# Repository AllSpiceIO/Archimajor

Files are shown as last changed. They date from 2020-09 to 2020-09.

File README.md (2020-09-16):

**Note**: The information contained below does not necessarily reflect the design intent for this board, nor the true characteristics of the design. Rather, this is intended to be a proof of concept for electrical project architecture.




[*](./README.md#Disclaimer)

# Archimajor

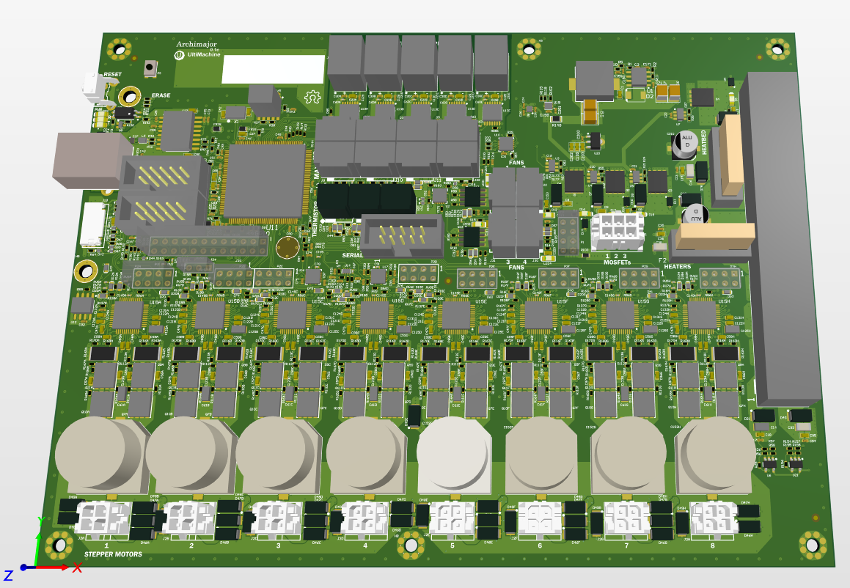
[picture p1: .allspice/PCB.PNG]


## Summary

3D printer motherboard, designed by [Ultimachine](https://ultimachine.com/). Features include:

- **5x integrated 256 microstep motor drivers**
- **6x PWM Mosfet outputs**
- **4x thermistor inputs**
- **SPI (Serial Peripheral Interface)**

---

## Specifications

### General Specifications

**Input Power Supply**: 12V - 24V DC, 16A+

**Operating Temperature Range (est.)**: 0dC ~ 70dC

## Firmware

[Source](https://github.com/ultimachine/Marlin4due/tree/Archim2)

[Binary](https://github.com/MarlinFirmware/Marlin/archive/bugfix-2.0.x.zip)

## Bill of Materials

<details>
    <summary><b>[Click to show Bill of Materials]</b></summary>

| Description | Designator | Footprint | Quantity | MANUFACTURER # |
|---|---|---|---|---|
| CAP CER 0603 100nF 50V 10% X7R | C1, C15, C18, C23A, C23B, C23C, C23D, C23E, C36, C47A, C47B, C47C, C47D, C47E, C47F, C47G, C47H, C95, C121A, C121B, C121C, C121D, C121E, C121F, C121G, C121H, C122A, C122B, C122C, C122D, C122E, C122F, C122G, C122H, C199, C202, C203 | C0603 | 37 | C0603C104K5RACTU |
| CAP CER 0.1UF 6.3V 10% X5R 0201 | C2, C60A, C60B, C60C, C60D, C60E, C62A, C62B, C62C, C62D, C62E, C67, C78, C91, C100, C105, C106, C149A, C149B, C149C, C149D, C149E, C149F, C149G, C149H, C204, C205, C206, C207, C208, C215, C217 | C0201 Large Pads | 32 | CL03A104KQ3NNNC |
| CAP CER 0402 TBD | C3 | C0402 | 1 | TBD |
| CAP CER 47UF 10V X5R 1210 | C4, C5 | C1210 | 2 | GRM32ER61A476KE20L |
| CAP CER 4.7UF 50V X7R 1210 | C6, C7 | C1210 | 2 | GRM32ER71H475KA88L |
| Capacitor Non Polarized | C8, C9, C10, C11, C27, C50, C153, C154, C209, C211 | C0603 | 10 | DNI-C0603TBD |
| CAP CER 10nF 50V X7R 0402 | C12A, C12B, C12C, C12D, C12E, C30A, C30B, C30C, C30D, C30E, C40, C43, C71, C77, C84, C86, C157, C158, C159, C160, C171, C214, C216 | C0402 | 23 | GRM155R71H103JA88D |
| 1000pF 50V Ceramic Capacitor X7R 0402 (1005 Metric) 0.039 L x 0.020 W (1.00mm x 0.50mm) | C13, C17, C35, C94 | C0402 | 4 | GRM155R71H102KA01D |
| CAP CER 10UF 50V 10% X5R 1206 | C14, C16, C38, C93 | C1206 | 4 | 490-10756-2-ND |
| CAP CER 0402 100nF 16V 10% X7R | C19, C20, C21, C22, C26, C28, C29, C31, C33, C39, C44, C45, C46, C51, C52, C54, C56, C63, C65, C66, C68, C69, C73, C76, C80, C81, C82, C92, C103, C155, C156, C161, C162, C164, C165, C166, C167, C169, C200, C201, C212, C213 | C0402 | 42 | GRM155R71C104KA88D |
| CAP CER 0402 1uF 6.3V 10% X5R | C24, C32, C34 | C0402 | 3 | GRM155R60J105KE19D |
| CAP ALUM 100UF 35V 20% SMD | C25, C210 | CAP-ELEC-063063077 | 2 | UWT1V101MCL1GS |
| CAP CER 10UF 6.3V 10% JB 0603 | C37, C53, C55, C57, C70, C72 | C0603 | 6 | C1608JB0J106K080AB |
| CAP CER 3PF 50V NP0 0603 | C41, C42 | C0603 | 2 | CL10C030BB8NNNC |
| CAP CER 0.22UF 50V X7R 0603 | C48A, C48B, C48C, C48D, C48E, C48F, C48G, C48H, C59A, C59B, C59C, C59D, C59E, C59F, C59G, C59H, C98A, C98B, C98C, C98D, C98E, C98F, C98G, C98H, C99A, C99B, C99C, C99D, C99E, C99F, C99G, C99H | C0603 | 32 | CGA3E3X7R1H224K080AB |
| CAP CER 10PF 50V 5% NP0 0402, 470nF 6.3v C0402 - GRM155R60J474KE19D | C49, C132A, C132B, C132C, C132D, C132E, C132F, C132G, C132H | C0402 | 9 | CL05C100JB5NNNC, GRM155R60J474KE19D |
| CAP CER 0603  1nF 50v 10% X7R | C58A, C58B, C58C, C58D, C58E, C58F, C58G, C58H, C96A, C96B, C96C, C96D, C96E, C96F, C96G, C96H, C97A, C97B, C97C, C97D, C97E, C97F, C97G, C97H, C123A, C123B, C123C, C123D, C123E, C123F, C123G, C123H | C0603 | 32 | C0603C102K5RACTU |
| CAP CER 1206 4.7uF 50V 10% X5R | C61A, C61B, C61C, C61D, C61E, C61F, C61G, C61H, C125A, C125B, C125C, C125D, C125E, C125F, C125G, C125H | C1206 | 16 | C1206C475K5PACTU |
| CAP CER 0402 TBD | C64, C74, C75, C79, C83, C85, C87, C88, C89, C90, C101, C102, C104 | C0402 | 13 | TBD |
| CAP CER 0.022UF 100V X7R 0603 | C124A, C124B, C124C, C124D, C124E, C124F, C124G, C124H | C0603 | 8 | C0603C223K1RACTU |
| CAP CER 4.7UF 6.3V X7R 0603 | C131A, C131B, C131C, C131D, C131E, C131F, C131G, C131H | C0603 | 8 | CL10B475KQ8NQNC |
| CAP CER 0402 2.2nF 25V C0G | C150 | C0402 | 1 | C0402C222J3GACTU |
| CAP CER 0402 22pF 50V 5% C0G | C151 | C0402 | 1 | 04025A220JAT2A |
| CAP ALUM 470UF 20% 50V SMD | C152A, C152B, C152C, C152D, C152E, C152F, C152G, C152H | CAP16x17 | 8 | UCZ1H471MNQ1MS |
| Capacitor Non Polarized | C198 | C0402 | 1 | DNI-C0402TBD |
| TVS DIODE 3.3VWM 10.4VC SOD923 | D1, D3, D13, D32, D33, D34, D35, D42, D58, D59, D64, D65, D66, D67, D68, D69, D71, D72, D73 | SOD923-100X40-2N | 19 | ESD9X3.3ST5G |
| DIODE SCHOTTKY 40V 5A SMB_DO214AA | D2 | SMB_DO-214AA_LRG | 1 | SK54B-LTP |
| DIODE TVS | D4, D10, D11, D14, D26 | SOD323-R | 5 | RSB39VTE-17 |
| DIODE SCHOTTKY 30V 200MA SOD523 | D5, D12A, D12B, D12C, D12D, D12E, D12F, D12G, D12H, D19A, D19B, D19C, D19D, D19E, D19F, D19G, D19H, D20A, D20B, D20C, D20D, D20E, D20F, D20G, D20H, D28, D29, D30, D31, D36, D37, D38, D39, D40, D41, D50, D51, D52, D53, D54, D55, D56, D57, D60, D61, D62, D63, D70, D74, D75, D76, D77 | SOD523_IPC | 52 | BAT54WX-TP |
| DIODE Schottky 3A SMA | D6, D7, D8, D15 | SMA-SM | 4 | SK310A |
| LED 0805 Red | D9, D16, D17, D18, D24, LED1, LED2, LED3, LED4 | LED2012120 | 9 | 5988110107F |
| TVS DIODE 24V 38.9V SMA | D21, D22, D43, D46A, D46B, D46C, D46D, D46E, D46F, D46G, D46H, D47A, D47B, D47C, D47D, D47E, D47F, D47G, D47H, D48A, D48B, D48C, D48D, D48E, D48F, D48G, D48H, D49A, D49B, D49C, D49D, D49E, D49F, D49G, D49H, D78 | SMA-SM | 36 | SMAJ24A |
| LED 0805 Green | D23 | LED2012120 | 1 | 5988170107F |
| LED 0805 Yellow | D25 | LED2012120 | 1 | 5988140107F |
| Rail-to-rail ESD protection devices | D27 | SOT886 | 1 | PRTR5V0U2F,115 |
| TVS DIODE 3.3VWM 10.4VC SOD923 | D44 | SOD923-D | 1 | ESD9X3.3ST5G |
| TVS DIODE 5V 9V SOD923 | D45 | SOD923-D | 1 | DF2S6.8FS,L3M |
| FUSE PTH ATO | F1, F2 | 3557 | 2 | 3557-2 |
| FERRITE BEAD 120 OHM 0603 1LN | FB26, FB27, FB28, FB29, FB30 | FB0603 | 5 | CIS10P121AC |
 | | FD1, FD2, FD3, FD4, FD5, FD6, FD7 | FIDUCIAL-1X2 | 7 | NOTAPART-Fiducial |
| Conn - 3mm Pitch Fixed | J1 | 43045-0612 | 1 | 0430450612 |
| Conn - 3mm Pitch Fixed | J2A, J2B, J2C, J2D, J2E, J2F, J2G, J2H | 43045-0412 | 8 | 43045-0412 |
| CONN BARRIER STRIP 10CIRC 0.325 | J3 | CON-Barrier-10-8.26mm | 1 | 4DB-P108-10 |
| 20021121-00010C4LF | J4 | FTSH-105-XX-X-DV | 1 | 20021121-00010C4LF |
| 3 Positions Header, Shrouded Connector 0.100 (2.54mm) Through Hole Gold - Pin in Paste | J5, J6, J7, J9, J10, J11, J22, J29, J30, J31, J32, J33 | 70543-02 PIN-IN-PASTE | 12 | 0705430002 |
 | | J8 | PN61729 | 1 | 61729-0010BLF |
| CONN HEADER VERT 10POS GOLD | J12, J13, J28 | HDR2X5 IDC | 3 | 302-S101 |
| Connector 2pos - Pin in Paste | J14, J15, J16 | 70543-01 PIN-IN-PASTE | 3 | 0705430001 |
| microSD 0475710001Molex Part | J18 | SD_MICRO 475710001 | 1 | 0475710001 |
| Header, 12-Pin, Dual row | J20 | HDR2X12 | 1 | 2213S-24G |
| TERM BLOCK 2POS 45DEG 3.5MM PCB | J21A, J21B, J21C, J21D, J21E | 1864286 | 5 | 1864286 |
| Header 3Pin 1Row T-Hole | J24 | HDR3X1 | 1 | 2211S-03G |
| FIXED IND 4.7UH 10A 15.5 MOHM | L1 | IND_10X10 | 1 | SRP1038A-4R7M |
| Common Mode Chokes Dual 90Ohm 100MHz 330mA 350mOhm DCR SMD | L5 | DLW21HN900SQ2L | 1 | DLW21HN900SQ2L |
| Header, 4-Pin, Dual row | P1, P2A, P2B, P2C, P2D, P2E, P2F, P2G, P2H | HDR2X4 | 9 | 2213S-08G, [NoParam] |
| MOSFET N-CH 40V 100A 8VSON | Q1, Q2, Q3, Q4 | SOT669_Universal | 4 | CSD18503Q5A |
| 40V 17 MOHM T6 S08FL DUAL | Q7A, Q7B, Q7C, Q7D, Q7E, Q7F, Q7G, Q7H, Q9A, Q9B, Q9C, Q9D, Q9E, Q9F, Q9G, Q9H, Q10A, Q10B, Q10C, Q10D, Q10E, Q10F, Q10G, Q10H, Q11A, Q11B, Q11C, Q11D, Q11E, Q11F, Q11G, Q11H | SO8FL-Dual | 32 | NVMFD5C478NT1G |
| TRANS NPN 60V 0.2A SOT523 | Q8 | SOT523 SMALL | 1 | MMBT3904T-7-F |
 | | Q12, Q13 | NCV8402AD-SOIC8 | 2 | NCV8402ADDR2G |
| RES SMD 10.2K OHM 1% 1/16W 0402 | R1 | R0402 | 1 | RC0402FR-0710K2L |
| RES SMD 1.4K OHM 1% 1/16W 0402 | R2 | R0402 | 1 | RMCF0402FT1K40 |
| RES 47 OHM 1% 1/16W 0402 | R3, R4, R13, R32, R59, R84, R86A, R86B, R86C, R86D, R86E, R86F, R86G, R86H, R88A, R88B, R88C, R88D, R88E, R89, R93, R94, R116A, R116B, R116C, R116D, R116E, R116F, R116G, R116H, R163A, R163B, R163C, R163D, R163E, R163F, R163G, R163H, R168A, R168B, R168C, R168D, R168E, R168F, R168G, R168H, R170A, R170B, R170C, R170D, R170E, R170F, R170G, R170H | R0402 | 54 | CRCW040247R0FKEDC |
| RES SMD 1.96K OHM 1% 1/16W 0402 | R5 | R0402 | 1 | RC0402FR-071K96L |
| RES SMD 10K OHM 1% 1/16W 0402 | R6, R7, R8, R9, R11, R12, R14, R15, R29, R30, R39, R54, R56, R64, R65, R66, R67, R68, R69, R70, R85, R95, R96, R97, R100, R101, R119, R150, R151, R155, R171, R182, R183 | R0402 | 33 | RC0402FR-0710KP |
| RES SMD 37.4K OHM 1% 1/16W 0402 | R10 | R0402 | 1 | RC0402FR-0737K4L |
| RES SMD 4.7K OHM 1% 1/16W 0402 | R16A, R16B, R16C, R16D, R16E, R16F, R16G, R16H, R18A, R18B, R18C, R18D, R18E, R18F, R18G, R18H, R62, R80, R90 | R0402 | 19 | RC0402FR-074K7L |
| Resistor | R17A, R17B, R17C, R17D, R17E, R17F, R17G, R17H, R60 | R0402 | 9 | DNI-R0402TBD |
| RES 0402 1k 63mW 1%, RES SMD 1K OHM 1% 1/16W 0402 | R19, R23, R33, R34, R36, R40, R41, R71, R72, R74, R76, R79, R102, R108A, R108B, R108C, R108D, R108E, R108F, R108G, R108H, R152, R174, R175, R176, R177, R186, R187, R188, R189, R191, R193, R197, R198 | R0402 | 34 | RC0402FR-071KL |
| RES SMD 100 OHM 1% 1/16W 0402 | R20, R21, R25, R53, R98, R99, R109, R114, R120, R133, R134, R135, R136, R137, R138, R139, R140, R141, R142, R143, R144, R145, R149, R153, R159, R160, R161, R180, R181 | R0402 | 29 | RC0402FR-07100RL |
| RES SMD 100K OHM 1% 1/16W 0402 | R22, R31, R35, R37, R38, R51, R58, R63, R73, R75, R78, R158, R190, R192 | R0402 | 14 | RC1005F104CS |
| RES SMD 10 OHM 1% 1/16W 0402 | R24, R27, R52, R55, R110A, R110B, R110C, R110D, R110E, R110F, R110G, R110H, R111A, R111B, R111C, R111D, R111E, R111F, R111G, R111H, R112A, R112B, R112C, R112D, R112E, R112F, R112G, R112H, R113A, R113B, R113C, R113D, R113E, R113F, R113G, R113H, R164A, R164B, R164C, R164D, R164E, R164F, R164G, R164H, R165A, R165B, R165C, R165D, R165E, R165F, R165G, R165H, R166A, R166B, R166C, R166D, R166E, R166F, R166G, R166H, R167A, R167B, R167C, R167D, R167E, R167F, R167G, R167H | R0402 | 68 | RC0402FR-0710RL |
| RES SMD 24K OHM 1% 1/16W 0402 | R26, R154 | R0402 | 2 | CRCW040224K0FKEDC |
| RES 0402 1M 100mW 5% | R28, R156 | R0402 | 2 | ERJ2GEJ105X |
| Res Thick Film 0402 24 Ohm 1% 0.063W | R42, R43, R45, R46, R47, R48, R77, R82, R83 | R0402 | 9 | RC0402FR-0724RL |
| RES SMD 2.37K OHM 1% 1/16W 0402 | R44, R50, R81, R87, R91, R92 | R0402 | 6 | RC0402FR-072K37L |
| RES SMD 6.8K OHM 1% 1/16W 0402 | R49 | R0402 | 1 | CRCW04026K80FKED |
| RES SMD 130K OHM 5% 1/16W 0402 | R57, R157 | R0402 | 2 | RC0402JR-07130KL |
| RES 0402 1M 100mW 5% | R61 | R0402TBD | 1 | ERJ2GEJ105X |
| RES SMD 0.0OHM JUMPER 1/10W 0603 | R103 | R0603 | 1 | CR0603-J/-000ELF |
| RES SMD 2.2 OHM 5% 1/16W 0402 | R107A, R107B, R107C, R107D, R107E, R107F, R107G, R107H | R0402 | 8 | RC0402JR-072R2L |
| RES SMD 15K 1% 1/16W 0402 | R115 | R0402 | 1 | RC1005F153CS |
| RES 0.01 OHM 1% 1/2W 0805 | R148 | R0805 | 1 | KRL1220E-M-R010-F-T5 |
| RES 0.05 OHM 1% 2W 2512 | R162A, R162B, R162C, R162D, R162E, R162F, R162G, R162H, R169A, R169B, R169C, R169D, R169E, R169F, R169G, R169H | R2512 | 16 | CSRN2512FK50L0 |
| RES SMD 1.8K OHM 1% 1/16W 0402 | R172, R173, R184, R185 | R0402 | 4 | RC0402FR-071K8L |
| VARISTOR 6.8V 10A 0201 | RV1, RV2, RV3, RV4, RV5A, RV5B, RV5C, RV5D, RV5E, RV5F, RV5G, RV5H, RV6A, RV6B, RV6C, RV6D, RV6E, RV6F, RV6G, RV6H, RV7A, RV7B, RV7C, RV7D, RV7E, RV7F, RV7G, RV7H | C0201 Large Pads | 28 | AVRM0603C6R8NT101N |
| SWTCH Momentary Washable | S1 | B3F-31XX | 1 | 1571610-2 |
| SWITCH TACTILE SPST-NO 0.05A 12V | S2 | KMR 6 Series | 1 | KMR741NG ULC LFS |
| IC REG BUCK ADJ 5A 8SOPWRPAD | U1 | SOIC127P600X170_HS | 1 | TPS54531DDAR |
| Quadruple Bus Buffer Gates With 3-State Outputs 14-VQFN -40 to 125 | U2, U10 | QFN50P350X350X100 | 2 | SN74AHCT125RGYR |
| MOSFET DRVR 3A 1-OUT High Speed Non-Inv6-Pin SOT-26 T/R | U3, U4, U5, U7 | SOT26P285X140 | 4 | ZXGD3009E6TA |
| IC QUAD DIFF COMPARATOR 14 -SOIC | U6, U21 | SOT23-5 | 2 | AP331AWG-7 |
| LDO 3.3V 500mA - low ESR Cout | U8 | TDFN1616-6LD-PL-1 | 1 | MIC5353-3.3YMT-TR |
| USB Opto Isolator | U9 | ADuM4160 | 1 | ADUM3160BRWZ-RL |
| Atmel | U11 | LQFP144_N | 1 | ATSAM3X8EA-AU |
| IC FLASH 16M SPI 104MHZ 8SOIC | U12 | S25FL216K0PMFI041 | 1 | AT25SF161-SSHD-T |
| IC CONV THERMOCOUPLE 14TSSOP | U13A, U13B, U13C, U13D, U13E | TSSOP-14L 65P640X110 | 5 | MAX31856MUD |
| Clock Fanout Buffer (Distribution) IC 1:4  8-XFDFN | U14 | XSON50P100X50-8L | 1 | 74AVC9112GTX |
| IC STEPPER MOTOR DVR TQFP48-EP | U15A, U15B, U15C, U15D, U15E, U15F, U15G, U15H | TQFP48-EP | 8 | TMC5160-TA |
| IC BUS BUFF TRI-ST QD 14VQFN | U16, U17 | PVQFN14_3.5X3.5 | 2 | SN74LVC125ARGYR |
| Optoisolator Transistor Output 3750Vrms 1 Channel 4-SO | U18 | SO-4 | 1 | TLP293(TPL,E |
| IC COMPARATOR BIDIR 8WSON | U19 | WSON8_2x2mm | 1 | INA381A2IDSGR |
| IC REG LINEAR 5V 100MA SOT89-3 | U20 | SOT-89-3 | 1 | L78L05ABUTR |
| Crystal 12MHz ±30ppm (Tol) ±50ppm (Stability) 13pF FUND 50Ohm | X1 | CRYS320500 | 1 | 405C35B12M00000 |

</details>

## Disclaimer

*NOTE: This does not represent actual data from the Rambo/Archimajor PCBA

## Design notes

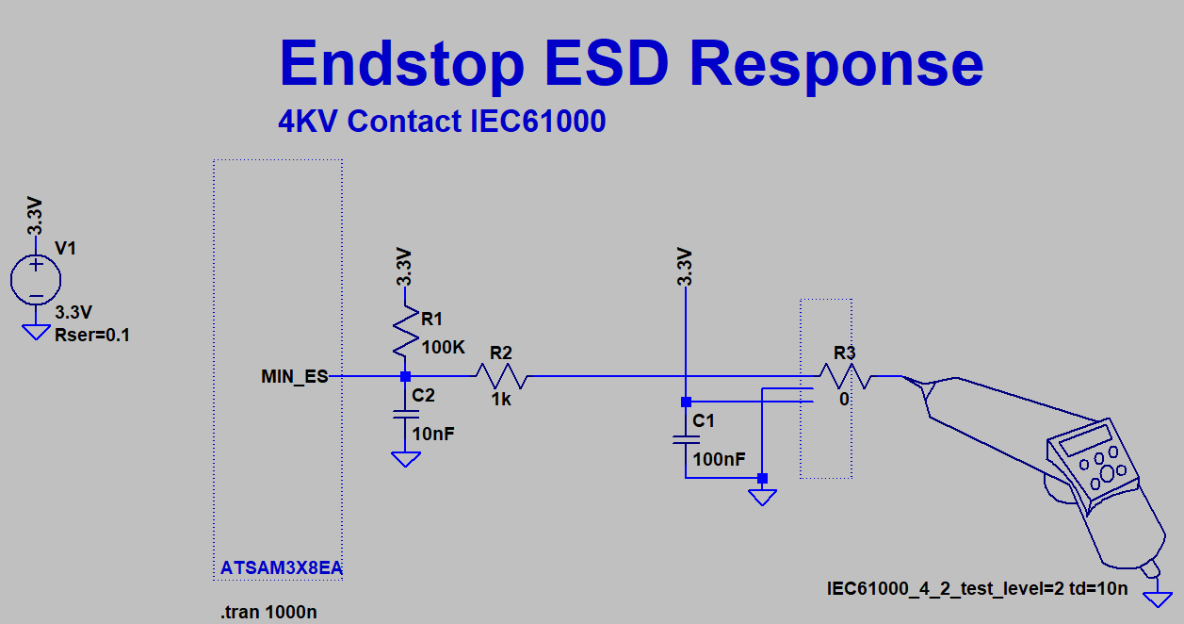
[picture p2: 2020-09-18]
Simulation/ESD/Endstops_ESD.PNG

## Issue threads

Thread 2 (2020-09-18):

Failing 4KV ESD Contact Discharge

kdumontnu, 2020-09-18:
*Disclaimer: The following data is fictional and does not represent real-world performance of the Archimajor Rambo Board*

### Summary
v0.4 of the Alpha main board fails required spec: 4KV contact discharge at endstop inputs.

Failure Mode(s): 10/10 cases SAM3X processor enters reset condition. 2/10 cases, memory is corrupted.

### Test setup
TBD

### Analysis
Atmel [SAM3X](https://ww1.microchip.com/downloads/en/DeviceDoc/Atmel-11057-32-bit-Cortex-M3-Microcontroller-SAM3X-SAM3A_Datasheet.pdf) (pg. 1378) specifies max VDDIO operating voltage of **4.0V**. Contact ESD discharge with no alternate ground path exceeds this value with significant energy content.

### Simulation Results

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

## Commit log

2018-12-04 add TMC5160 schematic and initial floorplan
    [Archim2.PrjPcb, Archim2_2.1a_PickPlace.csv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]
2018-12-07 Schematic Changelog: Renamed THERM_AN4 netname to TC_AN4 Deleted R96 between X-REF and PA6 Renamed X-REF netname to TC_AN5 Created TC_AN6 connected to PA2 Created TC_AN7 connected to PA3 Delete PA3_T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
    [Archimajor.PrjPcb, EndStops.SchDoc, Fans.SchDoc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]
2018-12-07 Performed Design Update operations. Updated part numbers for newer fan circuit. Added pull up to SD_MODE on TMC5160. Changed LED resistor to 10K on fans. Assigned designators for Fans. Updated TACH n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
    [EndStops.SchDoc, Fans.SchDoc, Microcontroller.SchDoc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]
2018-12-07 Saved project with Fans schematic. Passes Design Update.
    [Archimajor.PrjPcb]
2018-12-07 Updated motor SPI netnames to match hardware SPI0.
    [Microcontroller.SchDoc, Motor-X.SchDoc]
2018-12-07 Update Design step for updating SPI names
    [Microcontroller.SchDoc]
2018-12-07 Removed old netnames from Microcontroller schematic.
    [Microcontroller.SchDoc]
2018-12-29 add tmc5160 schematic and layout for X driver
    [Archimajor.PrjPcb, Archimajor.ods, Connectors.SchDoc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]
2018-12-31 add y, part z as independent schematics
    [Archimajor.PrjPcb, Connectors.SchDoc, Motor-E1.SchDoc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]
2019-01-02 refactor project. motors to multi channel design
    [Archimajor.PrjPcb, Archimajor.SchDoc, Archimajor.ods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]
2019-01-03 change motor connector and mosfets
    [Archimajor.SchDoc, Archimajor.ods, Connectors.SchDoc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]
2019-01-04 fix layout for seperate motor supplies
2019-01-07 add thermocouple schematic
    [Archimajor.PrjPcb, Archimajor.SchDoc, Connectors.SchDoc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]
2019-01-09 add thermocouples. layout and routing progress.
    [Archimajor.PrjPcb, Archimajor.SchDoc, Connectors.SchDoc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]
2019-01-11 more layout on motor driver 1
2019-01-21 add spi buffers
    [Archimajor.PrjPcb, Archimajor.SchDoc, Connectors.SchDoc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]
2019-01-30 place and fanout spi buffers. net routing
    [Archimajor.PrjPcb, Archimajor.SchDoc, Connectors.SchDoc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]
2019-02-01 driver layout cleanup
    [Microcontroller.SchDoc]
2019-02-07 route remaining major busses. route fans
    [Fans.SchDoc, Microcontroller.SchDoc, Mosfets.SchDoc]
2019-02-10 route heaters
    [Microcontroller.SchDoc, Mosfets.SchDoc]
2019-02-13 route mossfets, power input. cleanup silks
    [Archim2_2.1a_PickPlace.csv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]
2019-02-15 fan gate pull downs = 10K
    [Archimajor.PrjPcb, Fans.SchDoc]
2019-02-22 silk screen, misc cleanup
    [Archim_Panel.PcbDoc, Archim_Panel.PrjPcb, Archimajor.PrjPcb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]
2019-02-22 change to 2x 220uF capacitor per motor. gen bom.
    [Motors.SchDoc, Power.SchDoc]
2019-02-27 change motor bulk caps to 470uF. limit resistor between motor diags.
    [Microcontroller.SchDoc, Motors.SchDoc, Power.SchDoc]
2019-03-03 silk clean up. generate 0.1b gerbers
    [Archimajor.PrjPcb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]
2019-03-06 annotate schematic numbers. cleanup title block
    [Archimajor.PrjPcb, Archimajor.SchDoc, Connectors.SchDoc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]
2019-04-27 more accurate pin name for DCEN. Add mechanical output
    [Archimajor.PrjPcb, Motors.SchDoc]
2019-04-27 remove stale files. Now 0.1b
    [Archim 2.0a repin.ods, Archim.PcbLib, Archim_TF_Bottom.PcbDoc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]
2019-07-11 Non-pop R17 to disable DCEN. Needs to be populated or changed if encoders are desired
    [Motors.SchDoc]
2019-08-27 thatchs review patches. Increase mosfet pours on drivers, Erase too away from screw, signal to j28 pin9, straignten traces around D22, fix recursive mosi
    [Archimajor.PrjPcb, Microcontroller.SchDoc]
2020-05-05 Remove ESD Protection on Fan Input
    [Archimajor.PrjPcb, Fans.SchDoc]
2020-05-05 Add ESD protection to fan input
    [Fans.SchDoc]
2020-06-23 Add PcbDoc files to githook
2020-06-23 Revert to previous version of PCB (for demo)
2020-06-23 Place components for PCB (For Demo)
2020-07-07 Baseline PCB
2020-09-08 Reroute trace (demo)
2020-09-08 Add PCB to .gitattributes
2020-09-09 Add badges and PCB image
2020-09-18 Remove ESD protection (revert to base case)
    [EndStops.SchDoc]
